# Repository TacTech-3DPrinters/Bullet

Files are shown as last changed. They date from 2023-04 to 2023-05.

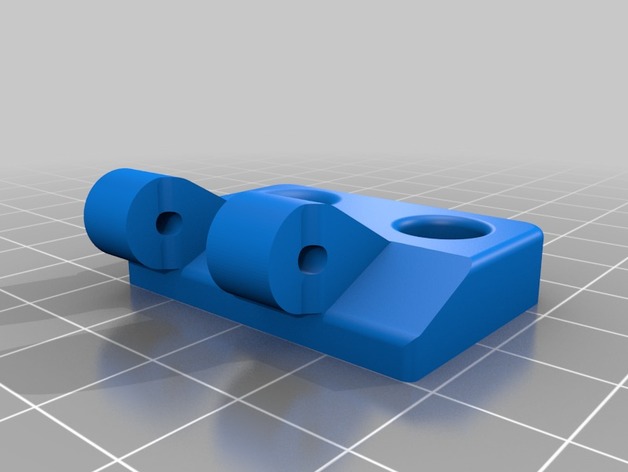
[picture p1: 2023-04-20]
printed-mods/IKEA_Lack_Enclosure_Creality_Ender_3/images/pan_head_left_hand.jpg

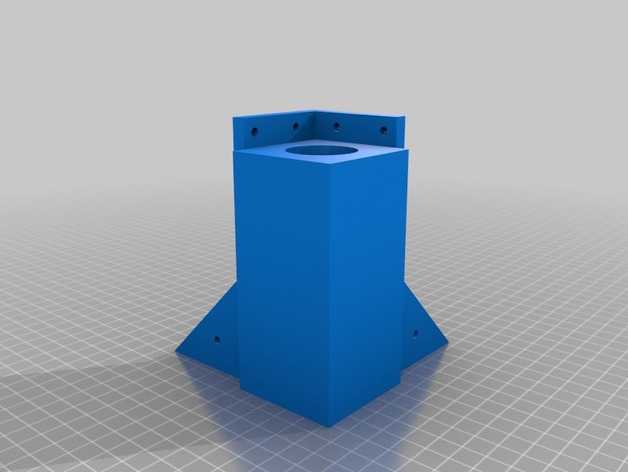
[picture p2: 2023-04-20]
printed-mods/IKEA_Lack_Enclosure_Creality_Ender_3/images/uprights_riser_completed_100mm.jpg

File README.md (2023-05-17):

# Bullet

Bullet is a heavily modified Ender3. All mods and software is tracked on this repository.

Bullet runs Klipper now! It also has two different control boards - the main control board, which is an SKR Mini E3 V1.2 and a toolhead control board connected over CAN, which is a BIQU EBB42. Here are the compiling + deployment instructions moving forward.

## Getting Started

This repo contains all the configs needed for Bullet to run and compile Klipper. Here are the instructions to get started (which may be upgraded to a script in the future:
``` bash
rm -rf $HOME/printer_data/config
ln -s $HOME/Bullet/klipper-configs $HOME/printer_data/config
```
Also will need to re-setup the CAN connection. See https://maz0r.github.io/klipper_canbus/controller/rs485.html

## Main Control Board - SKR Mini E3 V1.2

### Building and Deploying Manually

Run the following commands on the raspberry pi
``` bash
# Build the klipper firmware for the main control board
cd ~/klipper
make clean
make KCONFIG_CONFIG=$HOME/Bullet/control-board/BTT_SKR_Mini_E3_v3/klipper-make.cfg

# Stop the klipper service to upload to the control board
sudo service klipper stop

# Run the flashing script over the SD card
./scripts/flash-sd-card.sh /dev/serial/by-id/usb-Klipper_stm32g0b1xx_4F0047001250415833323520-if00 btt-skr-mini-e3-v3

# Restart the klipper service
sudo service klipper start
```

## Toolhead Board - Biqu EBB42 with MAX31856

### Initialization Steps
1. Set up CAN on Raspberry Pi. See https://maz0r.github.io/klipper_canbus/controller/rs485.html

2. Install CANBoot to allow for installing klipper over CAN

``` bash
# Clone CanBoot
cd ~
git clone https://github.com/Arksine/CanBoot

# Build CanBoot
cd CanBoot
make clean
make KCONFIG_CONFIG=$HOME/Bullet/control-board/BIQU_EBB42_v1_2/canboot-make.config

# Upload CanBoot
# Hold reset and boot buttons while plugged in over USB
# Verify the device is in bootloader mode with:
lsusb
# Flash the CanBoot firmware, make sure you replace the address at the end with what showed up in lsusb
sudo dfu-util -a 0 -D ~/CanBoot/out/canboot.bin --dfuse-address 0x08000000:force:mass-erase:leave -d 0483:df11
# For more information, see source below
```

Source: https://maz0r.github.io/klipper_canbus/toolhead/ebb36-42_v1.1.html

3. Flash Klipper over CAN

``` bash
# Make sure you see the device on the CAN network
~/klippy-env/bin/python ~/klipper/scripts/canbus_query.py can0

# Build the Klipper firmware for the toolhead board
cd ~/klipper
make clean
make KCONFIG_CONFIG=$HOME/Bullet/control-board/BIQU_EBB42_v1_2/klipper-make.config

# Flash the Klipper firmware on the toolhead board over CAN
# Replace the last parameter with the UUID from the canbus_query command above
python3 ~/CanBoot/scripts/flash_can.py -i can0 -f ~/klipper/out/klipper.bin -u 4c6771e6c940
```

Source: https://maz0r.github.io/klipper_canbus/toolhead/ebb36-42_v1.1.html

## Raspberry Pi 3B+
Making sure the Raspberry Pi won't overheat or undervolt due to too little power is super important. Use the following commands to run a worst-case scenaro CPU stress test, each for 10 minutes:

```bash
while true; do vcgencmd measure_clock arm; vcgencmd measure_temp; sleep 10; done& stress -c 4 -t 900s
while true; do vcgencmd measure_clock arm; vcgencmd measure_temp; sleep 10; done& ./cpuburn-a53
```
Source: https://core-electronics.com.au/guides/stress-testing-your-raspberry-pi/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,and%20stability%20of%20the%20system.

## Resources

* Connecting RPI to control board over UART: https://www.youtube.com/watch?v=AtW3GqkKUz8
* CANBUS board + RPI Hat instructions: https://www.youtube.com/watch?v=jgE3XMM9PBk
* Updating klipper on MCU automatically with a script: https://www.youtube.com/watch?v=uNW8phiV83w
* Voron Design documentation for skr mini e3 v1.2: https://docs.vorondesign.com/build/software/miniE3_v12_klipper.html
* Debugging CANBus communication issues: https://www.teamfdm.com/forums/topic/1524-debugging-canbus-and-communication-timeout-while-homingbytes_invalid/
* Sweet KlackEnder probe macros: https://github.com/Harrypulvirenti/Klack-Probe-Macros/tree/main

### Calibrating the 3D Printer
* Preflight checklist: https://github.com/Klipper3d/klipper/blob/master/docs/Config_checks.md
* 

### Board Documentation

* [BigTreeTech SKR E3 Mini V1.2 documentation](https://github.com/bigtreetech/BIGTREETECH-SKR-mini-E3), also found in `control-board/BTT_SKR_MINI_E3_V1_2`
* RS485 CANbus Raspberry Pi Hat: https://www.waveshare.com/rs485-can-hat.htm

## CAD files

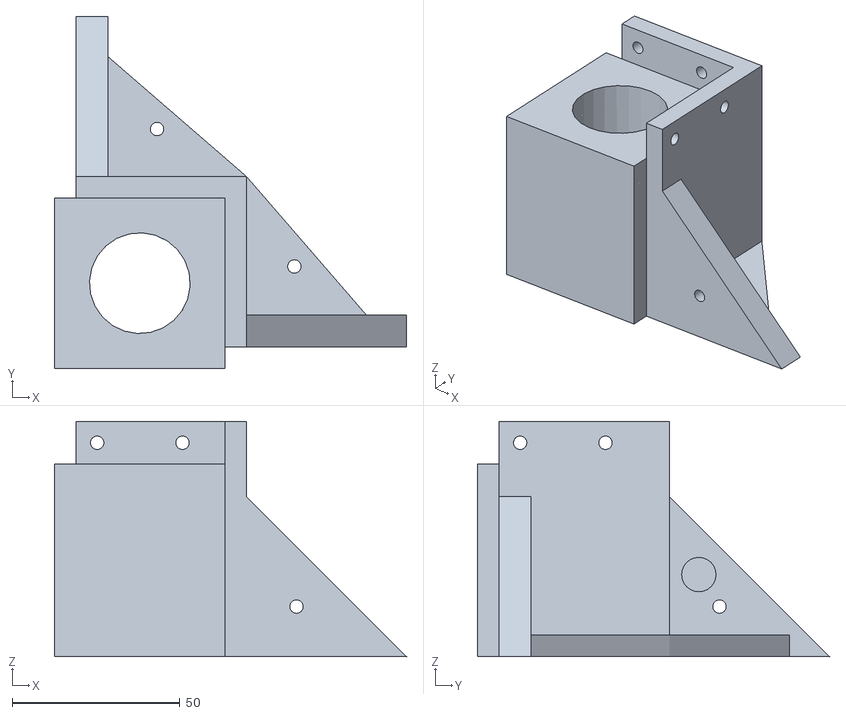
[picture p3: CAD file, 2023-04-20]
printed-mods/IKEA_Lack_Enclosure_Creality_Ender_3/files/uprights_complete_revised_70mm.stl
104.8 x 104.8 x 70.0

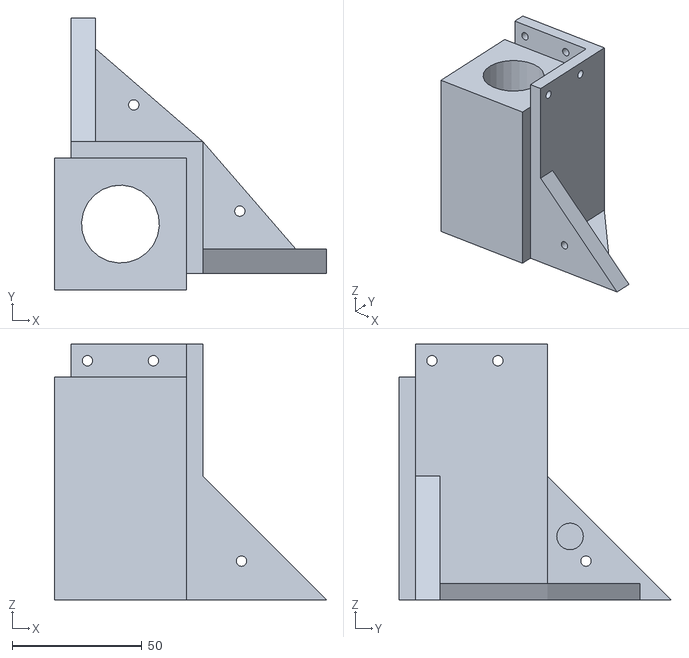
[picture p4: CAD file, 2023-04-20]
printed-mods/IKEA_Lack_Enclosure_Creality_Ender_3/files/uprights_complete_revised.stl
104.8 x 104.8 x 98.4

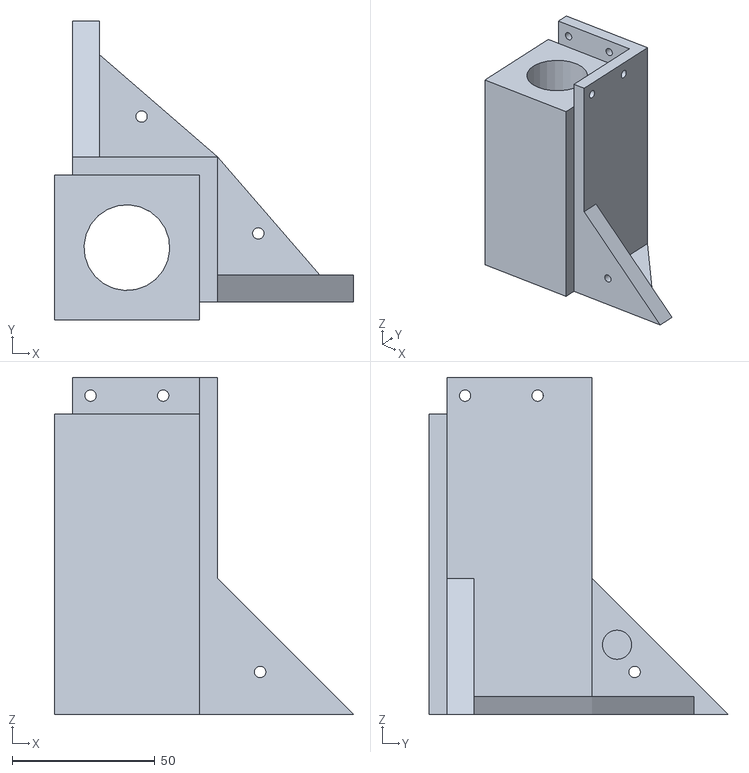
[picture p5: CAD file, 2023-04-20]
printed-mods/IKEA_Lack_Enclosure_Creality_Ender_3/files/uprights_riser_completed_100mm.stl
104.8 x 104.8 x 117.9

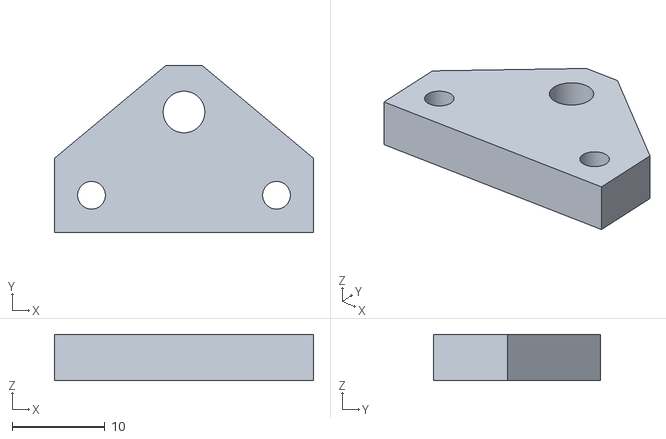
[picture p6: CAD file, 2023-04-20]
IMU_MPU_9265_Mount.stl
28.0 x 18.0 x 5.00

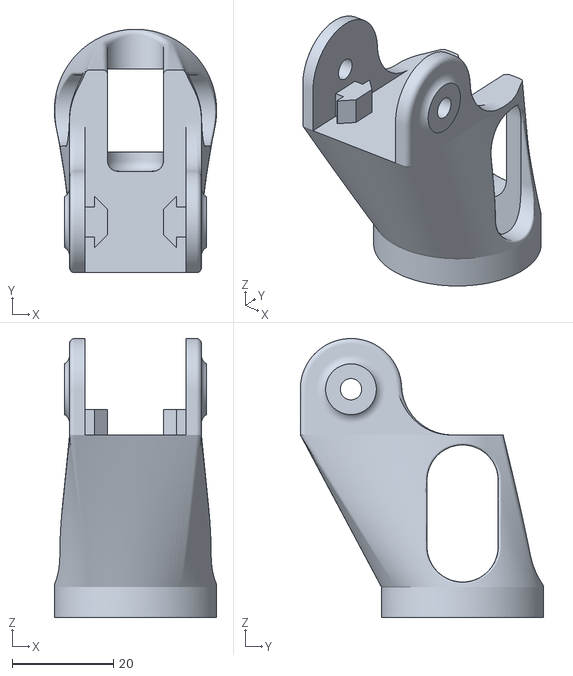
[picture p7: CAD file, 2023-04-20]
printed-mods/BeltTensioners/Ender3_YTensioner_Body.stl
32.0 x 48.0 x 55.0

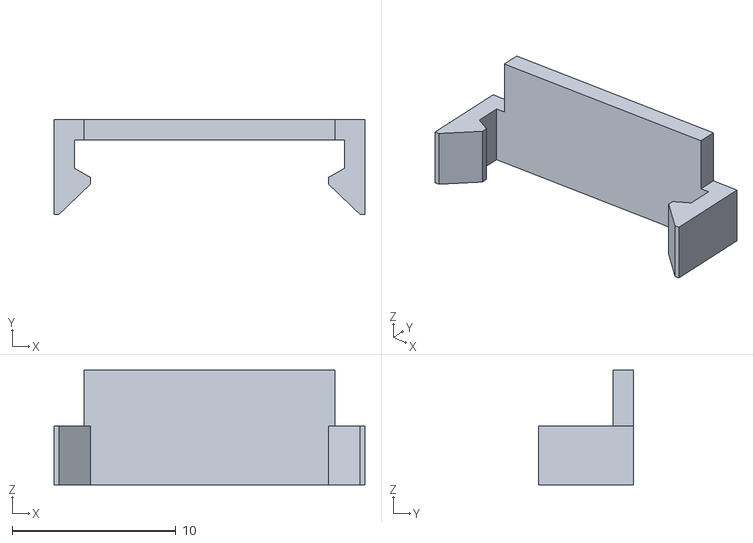
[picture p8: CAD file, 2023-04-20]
printed-mods/CableChain/slim-link_cover.stl
19.0 x 5.80 x 7.00

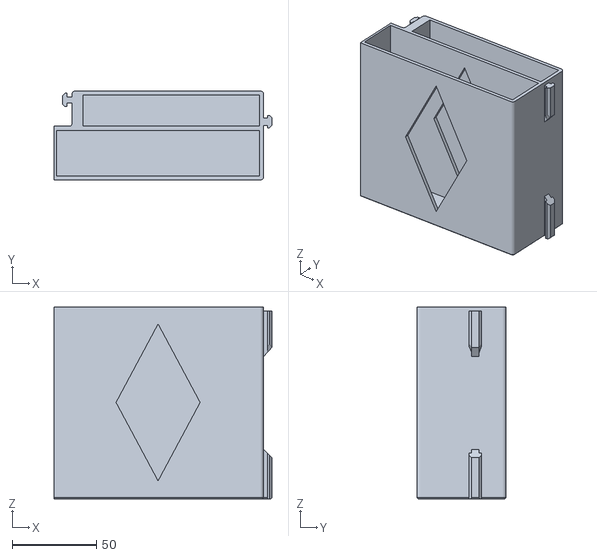
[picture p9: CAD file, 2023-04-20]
printed-mods/Drawers/Drawer_Case_RIGHT.stl
129.6 x 53.0 x 114.0

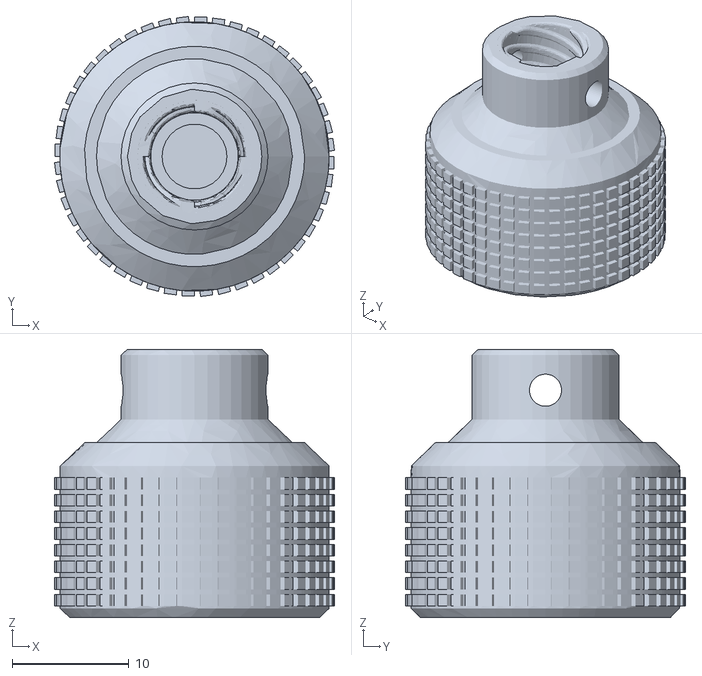
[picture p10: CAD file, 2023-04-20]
printed-mods/Ender3_ZAxis_Knob.stl
24.0 x 24.0 x 23.0

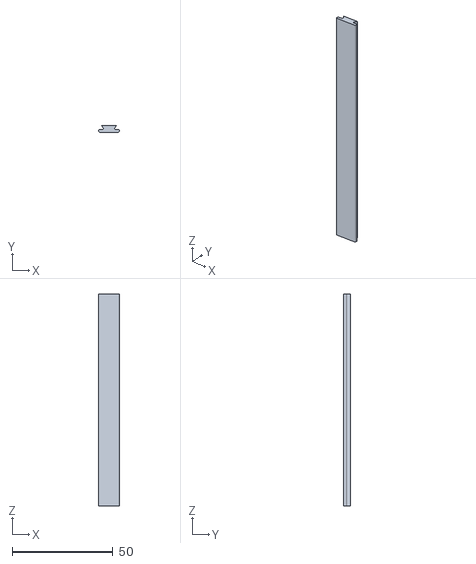
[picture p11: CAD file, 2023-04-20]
printed-mods/Ender_3_V_Slot_Covers/files/slot_cover_105mm.stl
10.2 x 3.23 x 105.0

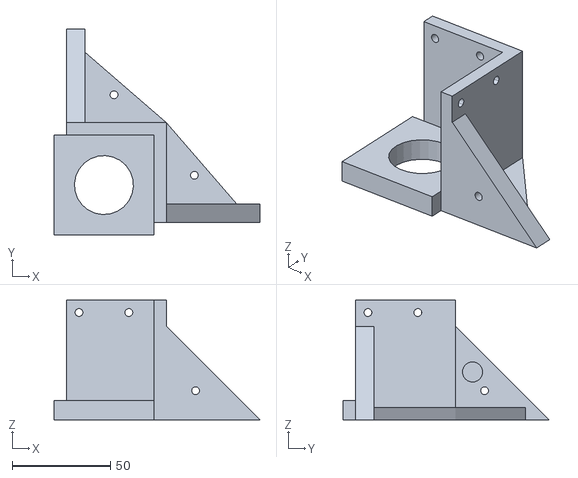
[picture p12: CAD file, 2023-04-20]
printed-mods/IKEA_Lack_Enclosure_Creality_Ender_3/files/uprights_riser_10mm.stl
104.8 x 104.8 x 61.0

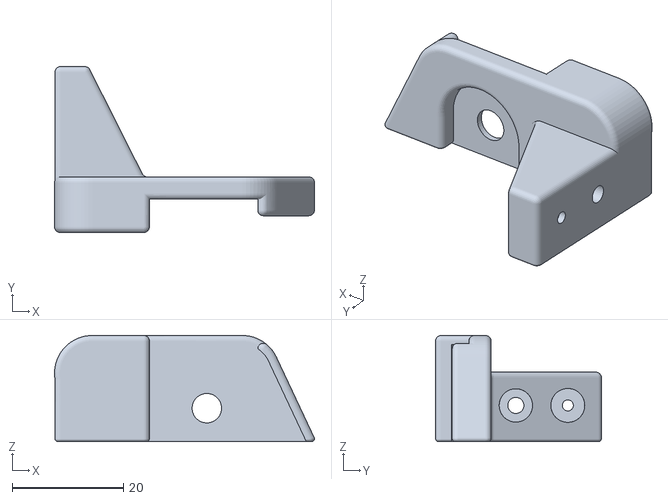
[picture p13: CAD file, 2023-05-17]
printed-mods/KlackEnder-Probe/STL/Ender 3 S1/Probe_Dock_S1.stl
46.8 x 29.9 x 19.1

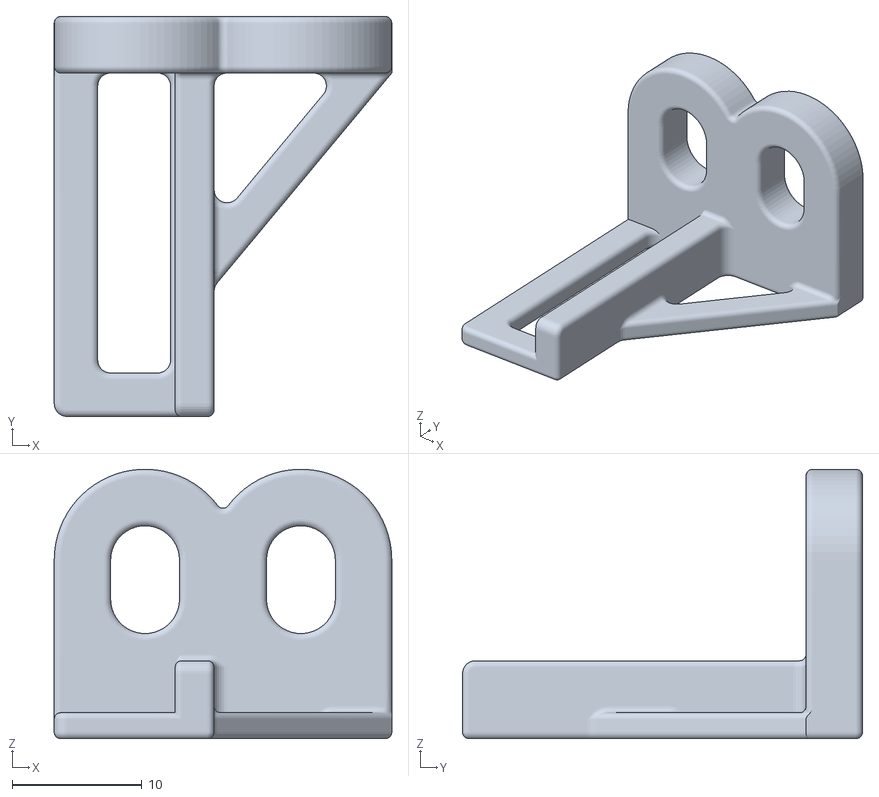
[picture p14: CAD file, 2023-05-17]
printed-mods/KlackEnder-Probe/STL/Probe_Retainer.stl
26.0 x 30.8 x 20.7

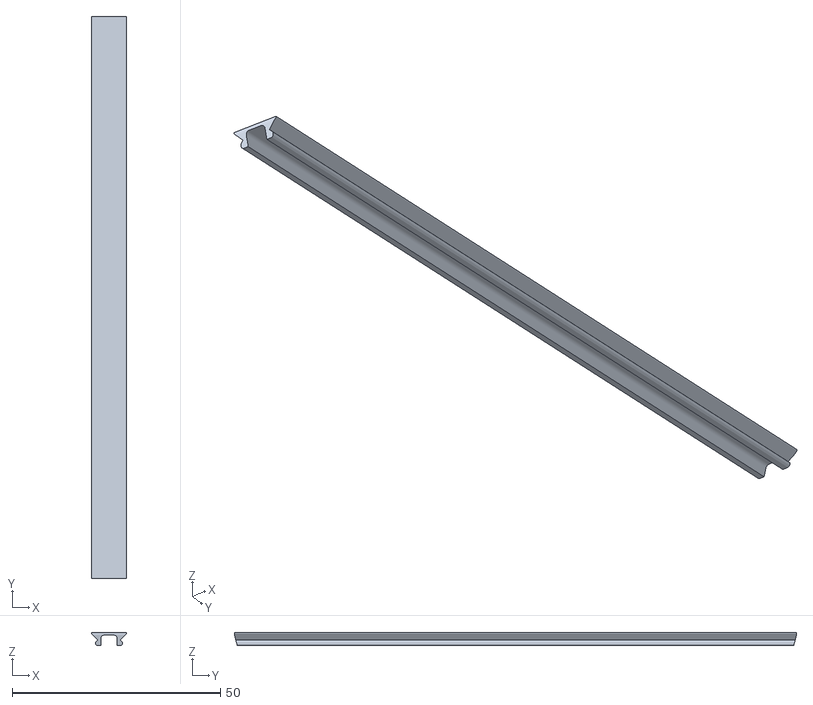
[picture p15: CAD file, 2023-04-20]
printed-mods/LED_Light_Bar/V-Slotcover135mmV2.stl
8.51 x 135.0 x 3.12

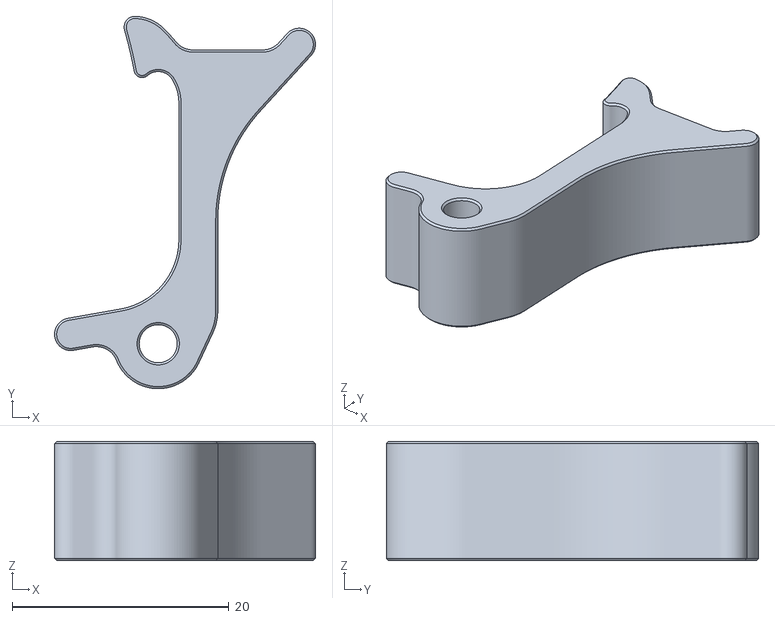
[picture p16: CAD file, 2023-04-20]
printed-mods/VoronAfterburner/[a]_latch.stl
24.1 x 34.3 x 11.0

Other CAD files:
test-prints/temp-tower-190-230.stl
printed-mods/2020Cap.stl
printed-mods/BeltTensioners/Ender3_XTensioner_Center.stl
printed-mods/BeltTensioners/Ender3_XTensioner_Body.stl
printed-mods/BeltTensioners/Ender3_XTensioner_Head.stl
printed-mods/CableChain/cableChain_link_v3.stl
printed-mods/CableChain/extruder-mount-27mm-alu.stl
printed-mods/CableChain/extruder-mount-27mm-stock.stl
printed-mods/CableChain/extruder-mount-32mm-alu-dd.stl
printed-mods/CableChain/slim-link.stl
printed-mods/Drawers/Drawer_Case_LEFT.stl
printed-mods/Ender_3_V_Slot_Covers/files/400mm_for_led_v1.stl
printed-mods/Ender_3_V_Slot_Covers/files/400mm_for_led_v2.stl
printed-mods/Ender_3_V_Slot_Covers/files/slot_cover_143mm_original.stl
printed-mods/Ender_3_V_Slot_Covers/files/slot_cover_165mm.stl
printed-mods/Ender_3_V_Slot_Covers/files/slot_cover_165mm_top_holes.stl
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

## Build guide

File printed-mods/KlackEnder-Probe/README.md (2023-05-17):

## KlackEnder Probe

KlackEnder Probe - **Simple, fast and cheap!**

<table>
  <tr>
    <td> </td>
    <td> </td>
  </tr>
</table>

### What is this about?

Adaptation of the [Klicky](https://github.com/jlas1/Klicky-Probe)/[Quickdraw](https://github.com/Annex-Engineering/Quickdraw_Probe) Probe for the Ender 3 and comparable Creality printers. The probe is compatible with all printers that use the X plate of the Ender 3 and cost of the probe is <10€, of which the switch is the most expensive part.
The probe is compatible with Marlin and Klipper. Both firmwares work with the G29 command, the docking is done automatically by the printer, it couldn't be easier! Both firmwares add a KlackEnder menu to the display that can be used to dock and undock the Probe. The Bed-Mesh can be created via the custom menu, via the default firmware settings or with G29.

### Is it compatible with my printer?

As long as your printer uses a X-Axis plate that's similar to the one of the Ender 3: **YES!***
* You might have to adapt the parts (slightly) if you're not using an Ender 3 or the stock x-plate. See the Basic-Check section to check the basic measurements and see if you printer is compatible. If not and you really struggle with CAD just ping me on my [Discord](https://discord.gg/xqpKrxt9FC) ;)

### Why should I build it?

Well, as with my other mods, the focus is on the best cost-benefit ratio. The KlackEnder is very cheap and very easy to build. No need to pay 40-50€ for a probe that is still affected by heat, takes forever to mesh, and causes a lot of headaches to wire. For the Klack it's: Print - assemble - mount - start printing, that's it. Especially with Klipper, setup couldn't be easier, just use my pre-made macros, copy and paste, hit restart and you're ready for the next print.

#### Quick Overview:

- Compatible with Marlin and Klipper. Easy setup - firmware changes provided.
- 100% automatic probe docking and undocking.
- 100% open source parametric design! With the supported CAD file and instructions, it couldn't be easier to customize the parts to your needs! Even if you've never worked with CAD before, I promise you can customize the parts any way you want!
- Custom menu to control the probe (not for Ender 3 V2 with Jyers GUI).
- The cheapest way to get a fast and very accurate probing ( sample range of 1-2 microsteps (0.000-0.005mm with 16 microsteps)
- Easy to install, no soldering, no complicated wiring
- Works with all pressure surfaces, not affected by heat, no heat soak required

If you have any questions feel free to join the [Discord-Server](https://discord.gg/xqpKrxt9FC).
 
<a href="https://discord.gg/xqpKrxt9FC">
         <img alt="Join" src="https://github.com/kevinakasam/BeltDrivenEnder3/blob/main/_ignore/Pictures/Discord-Logo%2BWordmark-Color.png"
         width=250" >
</a>

#### Parametric CAD Design

I always try my best to support a wide range of possible setups so you don't have to deal with CAD. With this design I have gone one step further: Not only does this design support a wide range of setups, but also the CAD is very easy to adapt for anyone, even if you've never worked with CAD before!

**How that? Parametric design!**

Parametric design means that everything is based on variables / parameters which you can easily change. The design itself adapts automatically to the changes you made. This may still sound a bit complicated, but trust me, with the detailed instructions I provide, it couldn't be easier! More about that on my [website](https://kevinakasam.com/lets-adapt-the-cad/).

## Bill of Materials + Instructions

As for my Belt-Mod, you can find all needed Hardware, STLs and instructions on my Website:

<a href="https://kevinakasam.com/klackender/">
         Guide
</a>

### STL-Files / Tolerances
<table>
  <tr>
    <td> </td>
    <td> </td>
  </tr>
</table>

Some people have contacted me with the problem that the layers split when they insert the magnets. This happens when the magnet is too big for the hole/the hole is too small for the magnet. So either the magnets are a bit bigger than 6mm or your printer prints the holes too small (never use a caliper to measure the magnets!. Only if they are made of plastic!). How the printer prints the holes depends not only on the material (ABS shrinks a bit, while PETG stays fairly constant) but also on the orientation of the holes. Vertical holes are usually a bit smaller than the horizontal ones, the ones that are printed in the walls. This is because these holes are formed by the layers and can never be completely round (the circle is made of 0.2mm (layer height) lines). At the same time, the diameter is strongly influenced by the print settings (speed, acceleration, linear advance/pressure advance, etc.).

However, you may need different tolerances than I do. That is why I have designed a small tolerance test (_thanks to SchlongkyDong for the idea!_). As already described, the tolerances for vertical and horizontal holes can/will differ. Stick a screwdriver through the smaller holes to get your magnets out again.

## Wiring Guide
Since there is no polarity on Switches, it doesn't matter which wire goes where. Just connect the switch to the two marked pins.
In the next chapter about firmware changes you will see where to add the pin.

Wiring for the Rev2 is very easy. Simply unmount/unplug your old z-endstop and connect the probe to the z-endstop port.

## Firmware Guide
The KlackEnder probe works with Marlin and Klipper. This guide only shows you what changes you need to make to the firmware, not how to modify/upload the firmware itself. There are several guides online for different boards and printers.
**You do not have to use the ```Probe In``` or ```Probe Out``` macros.** They're just a nice to have. The printer will do this automatically when you send a ```G29```.

### Klipper

The installation for Klipper is pretty easy. Simply do the changes below and copy the code from the ```KlackEnder.cfg```to your ```printer.cfg```
The ```[gcode_macro G29]``` does the same like the ```[gcode_macro AUTO_BED_MESH]```. I just added this so you can use the G29 command as usual.
#### Changes to the existing config:
```
[stepper_z]
endstop_pin: probe:z_virtual_endstop #if you want to use the Prove as z-endstop (You can unsinstall the stock z endstop then. If not, remive the [homing_override])
#position_endstop: 0 #remove this or uncomment it with a #
position_min: -8 # set a negative value (minimum as the probe z_offset)

[stepper_x]
position_max: 250 #Your printhead have to move all the way to the right to pickup the probe. If your screw collides with the metal plate, simply flip it around.

##Following does not apply for the E3-V2##
[stepper_y]
position_min: -8 #most Ender 3 configs have this wrong. Between the nozzle and the bed is a gap of 8mm (Y dimension) when the printer is homed. If not adapt this and the -8 in the Probe_In Makro). 
position_endstop: -8

```
#### Add new config:

**Don't forgot to edit your probe Pin:**
  ```
  ##################################
## Add this to your printer.cfg ##
##################################
#####################################################################
# KlackEnder- Settings
#####################################################################

# !! Change your Z endstop pin from 'endstop_pin: Pin123' to 'endstop_pin: probe:z_virtual_endstop'
# !! Also add in [stepper_y] 'position_min: -8'. Idk why but most configs mave this wrong. For the Stock Ender 3 the homed Y position is -8.

[probe]
pin: ^PC14 #Probe-Stop Connection on Skr Mini E3 V1.2
z_offset: 0 #Measure per your specific setup
x_offset: 4 # negative = left of the nozzle
y_offset: 21 # negative = in front of of the nozzle
speed: 5.0
lift_speed: 15.0
sample_retract_dist: 1
samples: 2
samples_tolerance_retries: 6

##[(7x7)-1] / 2 = 24
##[(5x5)-1] / 2 = 12
[bed_mesh]
speed: 300
horizontal_move_z: 2
mesh_min: 8,30
mesh_max: 223,201
probe_count: 5,5
relative_reference_index: 12
algorithm: bicubic
fade_start: 1
fade_end: 10
#fade_target:
#   The z position in which fade should converge. When this value is set
#   to a non-zero value it must be within the range of z-values in the mesh.
#   Users that wish to converge to the z homing position should set this to 0.
#   Default is the average z value of the mesh.
split_delta_z: 0.015
#   The amount of Z difference (in mm) along a move that will
#   trigger a split. Default is .025.
move_check_distance: 3
#   The distance (in mm) along a move to check for split_delta_z.
#   This is also the minimum length that a move can be split. Default
#   is 5.0.
mesh_pps: 4,4
#   A comma separated pair of integers (X,Y) defining the number of
#   points per segment to interpolate in the mesh along each axis. A
#   "segment" can be defined as the space between each probed
#   point. The user may enter a single value which will be applied
#   to both axes.  Default is 2,2.
#bicubic_tension: .2
#   When using the bicubic algorithm the tension parameter above
#   may be applied to change the amount of slope interpolated.
#   Larger numbers will increase the amount of slope, which
#   results in more curvature in the mesh. Default is .2.

[homing_override]
set_position_z:0 # Make printer think Z axis is at zero, so we can force a move upwards away from build plate
gcode:
    G90
    G1 Z10 F3000 ; move up to prevent accidentally scratching build plate    
    G28 X
    G28 Y
    PROBE_OUT
    G1 X117 Y117 F6000
    G28 Z
    PROBE_IN

##For Dual Z setups only!! (with independent motors, no Y splitters or dual Z port on board!)##
[z_tilt]
z_positions:
    25,117
    210,117
#   A list of X, Y coordinates (one per line; subsequent lines
#   indented) describing the location of each bed "pivot point". The
#   "pivot point" is the point where the bed attaches to the given Z
#   stepper. It is described using nozzle coordinates (the X, Y position
#   of the nozzle if it could move directly above the point). The
#   first entry corresponds to stepper_z, the second to stepper_z1,
#   the third to stepper_z2, etc. This parameter must be provided.
points:
    4,96.5
    219,96.5
#   A list of X, Y coordinates (one per line; subsequent lines
#   indented) that should be probed during a Z_TILT_ADJUST command.
#   Specify coordinates of the nozzle and be sure the probe is above
#   the bed at the given nozzle coordinates. This parameter must be
#   provided.
speed: 100
#   The speed (in mm/s) of non-probing moves during the calibration.
#   The default is 50.
horizontal_move_z: 15
#   The height (in mm) that the head should be commanded to move to
#   just prior to starting a probe operation. The default is 5.
retries: 10
#   Number of times to retry if the probed points aren't within
#   tolerance.
retry_tolerance: 0.01
#   If retries are enabled then retry if largest and smallest probed
#   points differ more than retry_tolerance. Note the smallest unit of
#   change here would be a single step. However if you are probing
#   more points than steppers then you will likely have a fixed
#   minimum value for the range of probed points which you can learn
#   by observing command output.

#####################################################################
# KlackEnder- Macros
#####################################################################

[gcode_macro PROBE_OUT]
gcode:
    G90
    G1 X245 F4000
    G4 P300
    G1 Z15
    G1 X0

[gcode_macro PROBE_IN]
gcode:
    G90
    G1 Z20
    G1 X245 F20000
    G1 Y-8
    G1 Z0
    G4 P300
    G1 X220 F6000
    G1 Z10
    G1 X0

[gcode_macro AUTO_BED_MESH]
gcode:
    PROBE_OUT
    BED_MESH_CALIBRATE
    #G1 Y0 F20000
    PROBE_IN

[gcode_macro G29]
gcode:
    PROBE_OUT
    BED_MESH_CALIBRATE
    #G1 Y0 F20000
    PROBE_IN

[gcode_macro Accuracy_Test]
gcode:
    PROBE_OUT
    G90
    G1 Y120 X120 F20000
    PROBE_ACCURACY
    PROBE_IN

[gcode_macro AUTO_Z_TILT_ADJUST]
gcode:
    PROBE_OUT
    Z_TILT_ADJUST
    PROBE_IN

#####################################################################
# KlackEnder- Menu - Only if you have a display installed!
#####################################################################

[menu __main]
type: list
name: Main

[menu __main __KlackEnder]
type: list
enable: True
name: KlackEnder

[menu __main __KlackEnder __ProbeOut]
type: command
name: Probe Out
gcode:
    PROBE_OUT

[menu __main __KlackEnder __ProbeIn]
type: command
name: Probe In
gcode:
    PROBE_IN

[menu __main __KlackEnder __AutoBedMesh]
type: command
name: Auto Bed Mesh
gcode:
    G28
    AUTO_BED_MESH
  ```

### Marlin
The installation for Marlin requires some more changes, but I will guide you through this :). These changes are only to get the KlackEnder working correctly. You still need to configure the rest of the options as appropriate for your printer. Support for the KlackEnder and similar probes was only recently added so a current version of Marlin needs to be used. Go to ```https://marlinfw.org/meta/download/``` and download the ```bugfix-2.1.x```. Follow the instructions for downloading, Installing, and configuring VSCode. Before compiling with PlatformIO you will need to setup your config files. Go to ```https://github.com/MarlinFirmware/Configurations/tree/bugfix-2.1.x/config/examples/Creality``` find your Printer/board setup and down load the appropriate Configuration.h & Configuration_adv.h. At this point you will want to go through and make the changes below, once completed you should be good to compile and use your printer. We are working on getting Configuration files posted for common printer combinations as well as .bins uploaded with pre-compiled firmware for common setups.

Marlin will now include a probe deploy and stow option under the motion menu when the Mag_mounted probe is defined.

#### 1. Configuration.h

- Search for ```//#define USE_PROBE_FOR_Z_HOMING``` and uncomment by removing ```//``` before ```#define```
- Search for ```#define PROBE_MANUALLY``` and if not commented out with ```//``` comment it out with ```//```
- If you have plugged your Probe into the Z-Endstop you will need to uncomment ```//#define Z_MIN_PROBE_USES_Z_MIN_ENDSTOP_PIN```
  If you have plugged your Probe into the probe port on your board you don't need to touch this.

- Search for ``` //#define MAG_MOUNTED_PROBE```  uncomment by removing the ```//```
  and change the following lines to
  ```
  #define MAG_MOUNTED_DEPLOY_1 { PROBE_DEPLOY_FEEDRATE, { 245, 114, 20 } }  // Move to side Dock / Attach probe
  #define MAG_MOUNTED_DEPLOY_2 { PROBE_DEPLOY_FEEDRATE, { 200, 114, 020} }  // Move probe off dock
  //#define MAG_MOUNTED_DEPLOY_3 { PROBE_DEPLOY_FEEDRATE, { 245, 114, 20 } }  // lift probe up
  //#define MAG_MOUNTED_DEPLOY_4 { PROBE_DEPLOY_FEEDRATE, {   0,   0,  0 } }  // Extra move if needed
  //#define MAG_MOUNTED_DEPLOY_5 { PROBE_DEPLOY_FEEDRATE, {   0,   0,  0 } }  // Extra move if needed
  #define MAG_MOUNTED_STOW_1   { PROBE_STOW_FEEDRATE,   { 245, 114, 20 } }  // Move to dock
  #define MAG_MOUNTED_STOW_2   { PROBE_STOW_FEEDRATE,   { 245, 114,  0 } }  // Place probe beside remover
  #define MAG_MOUNTED_STOW_3   { PROBE_STOW_FEEDRATE,   { 220, 114,  0 } }  // Side move to remove probe
  #define MAG_MOUNTED_STOW_4   { PROBE_STOW_FEEDRATE,   { 220, 114, 20 } }  // Ensure probe is off
  //#define MAG_MOUNTED_STOW_5   { PROBE_STOW_FEEDRATE,   {   0,   0,  0 } }  // Extra move if needed
  ```
  Probe deploy and stow feed rate can be changed by editing the appropriate lines

- Search for ```NOZZLE_TO_PROBE_OFFSET```  and change
  ```
  #define NOZZLE_TO_PROBE_OFFSET { 10, 10, 0 }

  // Most probes should stay away from the edges of the bed, but
  // with NOZZLE_AS_PROBE this can be negative for a wider probing area.
  #define PROBING_MARGIN 10
  ```

  to

  ```
  #define NOZZLE_TO_PROBE_OFFSET { 8, 21, 1.2 }   //--> set correct offset

  // Most probes should stay away from the edges of the bed, but
  // with NOZZLE_AS_PROBE this can be negative for a wider probing area.
  #define PROBING_MARGIN 15   //--> more clearance to the sides of the bed.
  ```
 
- Search for ```// @section geometry```  and change
  ```
  // The size of the printable area
  #define X_BED_SIZE 200
  #define Y_BED_SIZE 200

  // Travel limits (mm) after homing, corresponding to endstop positions.
  #define X_MIN_POS 0
  #define Y_MIN_POS 0
  #define Z_MIN_POS 0
  #define X_MAX_POS X_BED_SIZE
  #define Y_MAX_POS Y_BED_SIZE
  #define Z_MAX_POS 200
  ```

  For non Ender 3v2's

  ```
  // The size of the printable area
  #define X_BED_SIZE 230    //--> adjust bed size
  #define Y_BED_SIZE 235    //--> adjust bed size

  // Travel limits (mm) after homing, corresponding to endstop positions.
  #define X_MIN_POS 0
  #define Y_MIN_POS -8     //--> adjust endstop position
  #define Z_MIN_POS 0
  #define X_MAX_POS X_BED_SIZE +15     //--> adjust x travel
  #define Y_MAX_POS Y_BED_SIZE
  #define Z_MAX_POS 250     //--> adjust z travel
  ```
  For Ender 3v2's change it to
    ```
  // The size of the printable area
  #define X_BED_SIZE 230    //--> adjust bed size
  #define Y_BED_SIZE 228    //--> adjust bed size

  // Travel limits (mm) after homing, corresponding to endstop positions.
  #define X_MIN_POS 0
  #define Y_MIN_POS 0     //--> adjust endstop position
  #define Z_MIN_POS 0
  #define X_MAX_POS X_BED_SIZE +15     //--> adjust x travel
  #define Y_MAX_POS Y_BED_SIZE
  #define Z_MAX_POS 250     //--> adjust z travel
  ```
 
- Search for ```// @section calibrate```  and change
  ```
  //#define AUTO_BED_LEVELING_3POINT
  //#define AUTO_BED_LEVELING_LINEAR
  //#define AUTO_BED_LEVELING_BILINEAR
  //#define AUTO_BED_LEVELING_UBL
  //#define MESH_BED_LEVELING

  /**
  * Normally G28 leaves leveling disabled on completion. Enable one of
  * these options to restore the prior leveling state or to always enable
  * leveling immediately after G28.
  */
  //#define RESTORE_LEVELING_AFTER_G28
  //#define ENABLE_LEVELING_AFTER_G28
  ```

  to

  ```
  //#define AUTO_BED_LEVELING_3POINT
  //#define AUTO_BED_LEVELING_LINEAR
  //#define AUTO_BED_LEVELING_BILINEAR
  #define AUTO_BED_LEVELING_UBL     //--> Remove //
  //#define MESH_BED_LEVELING

  /**
  * Normally G28 leaves leveling disabled on completion. Enable one of
  * these options to restore the prior leveling state or to always enable
  * leveling immediately after G28.
  */
  #define RESTORE_LEVELING_AFTER_G28    //--> Remove //
  //#define ENABLE_LEVELING_AFTER_G28
  ```
 
- Search for ```Unified Bed Leveling```  
  Change  from ```#define MESH_INSET 1``` to ```#define MESH_INSET 10```
  Change   ```#define GRID_MAX_POINTS_X 10``` to ```#define GRID_MAX_POINTS_X 15```  
  Uncomment  by removing the ```//``` before ```#define UBL_MESH_WIZARD```  
  Uncomment  ```//#define LCD_BED_LEVELING```  
  Uncomment  ```//#define LCD_BED_TRAMMING```  
  Uncomment  ```//#define BED_TRAMMING_USE_PROBE```  
  Uncomment  ```//#define Z_SAFE_HOMING```  
  Uncomment  ```//#define EEPROM_INIT_NOW   // Init EEPROM on first boot after a new build```  

 - In Configuration_adv.H
  Uncomment ```//#define PROBE_OFFSET_WIZARD```

  ## Marlin Setup Before printing
  Go into the menu->Motion->Unified Bed Leveling->UBL Custom Bed Mesh
  set your normal bed temp and hotend temp and then select custom mesh. This will probe all points that can be reached by the probe and then interpolate the rest.
  
  ## Marlin Slicer Start Gcode
  In your slicer Gcode look for a line that says 
  ```G28```
  after that line add in the following two lines
  ```
  G29 L0 ; load mesh saved in slot 0 which is the default slot
  G29 A ; activate bed mesh leveling.
  G29 J ; Probe 3 points and tilt the mesh loaded in slot 0 to match the current bed tilt
  ```

### Rev_1 vs. Rev_2 (and Rev_2.x)

What's the difference between Revision 1 and Revion 2?
                   
The most important difference is the position of the probe. With the Rev2, the probe is attached to the X-axis, which is why the probe can be used as a Z end stop. So no additional port for an end stop is needed and the probe can simply be connected to the old Z endstop port. The renders below show the difference, the upper one is the Rev2. (The Probe mount on the hotendplate is the same for both version)
                   
<table>
  <tr>
    <td><img src="https://github.com/kevinakasam/KlackEnder-Probe/blob/main/Archive/Rev_2/Images/Comp.png" width="450"> </td>
    <td><img src="https://github.com/kevinakasam/KlackEnder-Probe/blob/main/Archive/Rev_2/Images/Comp2.png" width="450"> </td>
  </tr>
</table>

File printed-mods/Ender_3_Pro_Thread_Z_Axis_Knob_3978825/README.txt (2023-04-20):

Ender 3 Pro Thread Z Axis Knob by 3HappyOwls on Thingiverse: https://www.thingiverse.com/thing:3978825

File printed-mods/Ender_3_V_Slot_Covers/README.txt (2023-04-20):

Ender 3 Pro V-Slot covers by ximes on Thingiverse: https://www.thingiverse.com/thing:3379068

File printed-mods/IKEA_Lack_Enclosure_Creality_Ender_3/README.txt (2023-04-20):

IKEA Lack Enclosure Creality Ender 3 Compilation by Woody1978 on Thingiverse: https://www.thingiverse.com/thing:3083358

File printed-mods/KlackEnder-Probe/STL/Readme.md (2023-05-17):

All parts can be printed without supports. Just print them in the provided orientation.

**Print the tolerance test first!**
All horizontal holes have a tolerance of 0.2mm, all vertical ones have no tolerance. This should fit most printers and give you a tight fit. If the fit isn't right use the provided CAD files to change the tolerance. The f3d file has paramters for that (Check out my [website](https://kevinakasam.com/lets-adapt-the-cad/)). You could also join the discord and I will send you a file with the tolerances you want.

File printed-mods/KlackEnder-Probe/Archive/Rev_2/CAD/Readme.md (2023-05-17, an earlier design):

All supported Step and Fusion 360 files. Feel free to modify the parts, but please upload them as remix to Thingiverse :)

Original file link:
Ender 3 Step: https://github.com/Creality3DPrinting/Ender-3/tree/master/Ender-3%20Mechanical

# How to change the tolerances

There is an f3d file in the CAD folder. This file format is for Autodesk Fusion 360, a free CAD program for private users. You can use it to adjust the tolerances if the STL files I provided do not fit.
As described in the tolerance test, there are different tolerances for vertical and horizontal holes. Follow the steps below to create your own STL.

## 1: Open the fusion file
First you have upload the file to fusion. Simply double click on the file or upload it to the browser in fusion on the left side (once you opended a folder e.g `My First Project` theres a small blue upload option at the very top). Then open the file, it should look close to this:



## 2: Open the parameters tab

Click on the `MODIFY`dropdown and select the parameters option.



## 3: Change the parameters

Double click on the value you want to change.



## 4: Find the file you want to export

Find the file you want to export in the browser on the left side. You can expand the folders by clicking on the small triangles. (You can also double click on the file in the CAD window, right click on it and select `Find In Browser`at the very end of the menu).



## 5: Export the STL

Once you found the file you want to export, right click on it and select `Save As Mesh`.



## 6: Save the STL

Simply confirm the small dialog on the right by clicking `OK`. Select a place on you PC to save it, that's all :)



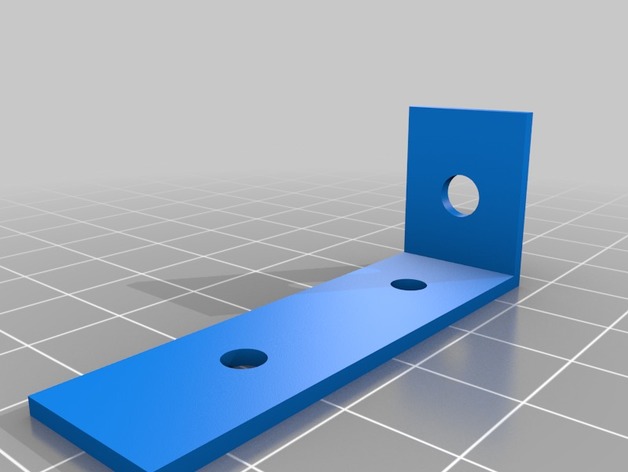
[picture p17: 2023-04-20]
printed-mods/IKEA_Lack_Enclosure_Creality_Ender_3/images/24V_PSU_holder.jpg

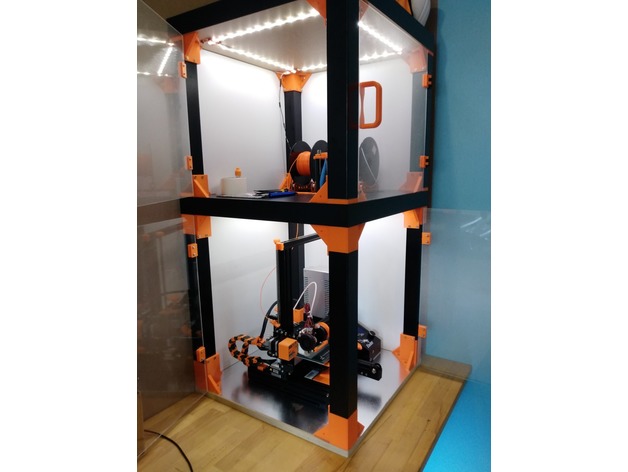
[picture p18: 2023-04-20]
printed-mods/IKEA_Lack_Enclosure_Creality_Ender_3/images/d2b5ca33bd970f64a6301fa75ae2eb22.jpg

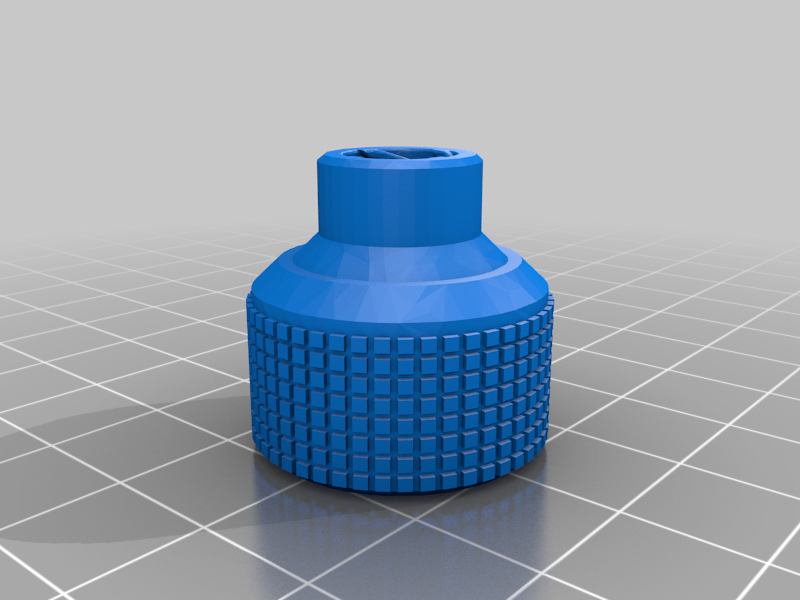
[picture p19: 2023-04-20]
printed-mods/Ender_3_Pro_Thread_Z_Axis_Knob_3978825/images/Ender3Pro_Threaded_Z_Axis_Knob.png

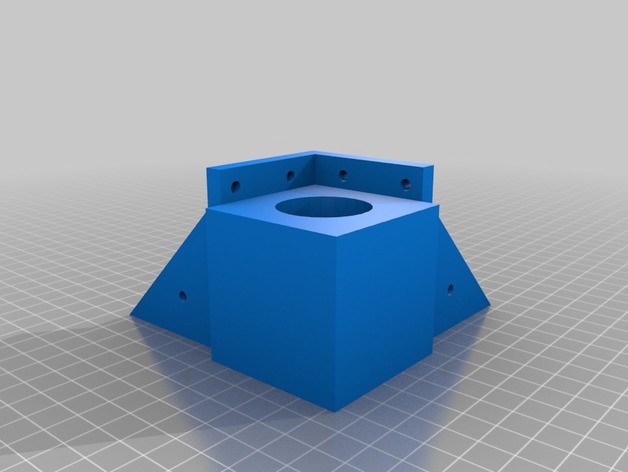
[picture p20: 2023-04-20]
printed-mods/IKEA_Lack_Enclosure_Creality_Ender_3/images/uprights_riser_50mm.jpg

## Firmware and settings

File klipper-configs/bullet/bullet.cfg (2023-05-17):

###########################################
########## Bullet Printer Config ##########
###########################################

# Include MainBoard
[include btt_skr_mini_e3_v3.cfg]

# Include Toolhead board
[include biqu_ebb42.cfg]

# Include RPI 3 Configuration
[include rpi3.cfg]

# Include g-code macros:
[include macros.cfg]

# Include KlackEnder macros
[include klackender.cfg]

# Include Accelerometer for input shaping
# comment out when not in use
# [include accel_mcu.cfg ]

#########################
##### Main Settings #####
#########################
[printer]
kinematics: cartesian
max_velocity: 300
max_accel: 3000
max_z_velocity: 5
max_z_accel: 100

# Controller Fan
[temperature_fan _controller_fan]
sensor_type: temperature_host
target_temp: 60
max_speed: 0.8
min_speed: 0.0
control: watermark
max_delta: 5
min_temp: 0
max_temp: 85

####################
##### Extruder #####
####################
[extruder]
rotation_distance: 23.500
gear_ratio: 3:1
nozzle_diameter: 0.600
filament_diameter: 1.750
sensor_type: NTC 100K MGB18-104F39050L32
control: pid
pid_Kp: 22.094
pid_Ki: 1.023
pid_Kd: 119.305
min_temp: 0
max_temp: 280
min_extrude_temp: 0
pressure_advance: 0.045

[heater_fan hotend_fan]
heater: extruder
heater_temp: 50
fan_speed: 0.8

[fan]
max_power: 1.0

######################
##### Heated Bed #####
######################
[heater_bed]
sensor_type: ATC Semitec 104GT-2
control: pid
pid_Kp: 70.445
pid_Ki: 0.968
pid_Kd: 1281.210
min_temp: 0
max_temp: 130

#################################
##### Z Home / Bed Leveling #####
#################################

[homing_override]
axes: z
set_position_z: 0
gcode:
    G90                 ; Absolute positioning
    G1 Z5 F3000         ; move up to prevent accidentally scratching build plate

    {% if printer.toolhead.homed_axes != "xyz" %}
        ; Test against xyz (not xy) because we assert z=0 at the beginning (set_position_z: 0)
        G28 X Y         ; Home X and Y
    {% endif %}

    PROBE_OUT
    G1 X98 Y85 F6000    ; Move to home Z position
    G28 Z               ; Home Z
    PROBE_IN

[probe]
pin: ^EBBCan: PB6
x_offset: 19
y_offset: 32
z_offset: 1.35
speed: 2.5
lift_speed: 15.0
sample_retract_dist: 1.0
samples: 2

[bed_mesh]
speed: 100
horizontal_move_z: 5
mesh_min: 25, 25
mesh_max: 210, 210
probe_count: 5,5
fade_start: 1
fade_end: 10
fade_target: 0

[z_tilt]
# Positions/points were chosen based on the probing position to be
#   - aligned with the bed mounting screws in the +/- X direction
#   - between the bed mounting screws in the +/- Y direction, same as probe y_offset
z_positions:
    -30, 85
    265, 85
points:
    15, 85
    185, 85
speed: 100
horizontal_move_z: 5
retries: 20
retry_tolerance: 0.01

###################################
#### Additional Stepper Motor #####
###################################
[stepper_x]
rotation_distance: 40
position_endstop: -15
position_min: -15
position_max: 235
homing_speed: 50

[stepper_y]
rotation_distance: 40
position_endstop: -15
position_min: -15
position_max: 220
homing_speed: 50

[stepper_z]
rotation_distance: 8
position_min: -6
position_max: 200
endstop_pin: probe:z_virtual_endstop

[stepper_z1]
rotation_distance: 8

#######################
##### Other Stuff #####
#######################

# Overhead lights
[neopixel overhead_lights]
chain_count: 13
color_order: GRB
initial_RED: 0.9
initial_GREEN: 0.9
initial_BLUE: 0.9

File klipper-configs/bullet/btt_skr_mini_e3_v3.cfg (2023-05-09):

# This file contains common pin mappings for the BIGTREETECH SKR mini
# E3 v3.0. To use this config, the firmware should be compiled for the
# STM32G0B1 with a "8KiB bootloader" and USB communication/USART.

# The "make flash" command does not work on the SKR mini E3. Instead,
# after running "make", copy the generated "out/klipper.bin" file to a
# file named "firmware.bin" on an SD card and then restart the SKR
# mini E3 with that SD card.

# See docs/Config_Reference.md for a description of parameters.

[mcu]
serial: /dev/serial/by-id/usb-Klipper_stm32g0b1xx_4F0047001250415833323520-if00

[temperature_sensor mcu_temp_sensor]
sensor_type: temperature_mcu
sensor_mcu: mcu

# [bltouch]
# sensor_pin: PC14
# control_pin: PA1

###################
##### X Motor #####
###################
[stepper_x]
step_pin: PB13
dir_pin: !PB12
enable_pin: !PB14
microsteps: 16
rotation_distance: 40
endstop_pin: ^PC0

[tmc2209 stepper_x]
uart_pin: PC11
tx_pin: PC10
uart_address: 0
run_current: 0.580
hold_current: 0.500
stealthchop_threshold: 999999

###################
##### Y Motor #####
###################
[stepper_y]
step_pin: PB10
dir_pin: !PB2
enable_pin: !PB11
microsteps: 16
rotation_distance: 40
endstop_pin: ^PC1

[tmc2209 stepper_y]
uart_pin: PC11
tx_pin: PC10
uart_address: 2
run_current: 0.580
hold_current: 0.500
stealthchop_threshold: 999999

###################
##### Z Motor #####
###################
[stepper_z]
step_pin: PB0
dir_pin: PC5
enable_pin: !PB1
microsteps: 16
rotation_distance: 8

[tmc2209 stepper_z]
uart_pin: PC11
tx_pin: PC10
uart_address: 1
run_current: 0.580
hold_current: 0.500
stealthchop_threshold: 999999

##########################
##### Extruder Motor #####
##########################
# These are normally extruder
[stepper_z1]
step_pin: PB3
dir_pin: PB4
enable_pin: !PD1
microsteps: 16
rotation_distance: 8

[tmc2209 stepper_z1]
uart_pin: PC11
tx_pin: PC10
uart_address: 3
run_current: 0.3
hold_current: 0.2
stealthchop_threshold: 999999

##############################
##### Extruder / Heatbed #####
##############################

# [extruder]
# heater_pin: PC8
# sensor_pin: PA0

[heater_bed]
heater_pin: PC9
sensor_pin: PC4

#############################
##### Fan Configuration #####
#############################
# FAN 0:
# [heater_fan e0_hotend_fan]
# pin: PC6

# FAN 1:
# [fan]
# pin: PC7

# FAN 2:
[temperature_fan _controller_fan]
pin: PB15

######################################
##### Extra Board Configurations #####
######################################

[neopixel overhead_lights]
pin: PA8

[board_pins]
aliases:
    # EXP1 header
    EXP1_1=PB5,  EXP1_3=PA9,   EXP1_5=PA10, EXP1_7=PB8, EXP1_9=<GND>,
    EXP1_2=PA15, EXP1_4=<RST>, EXP1_6=PB9,  EXP1_8=PD6, EXP1_10=<5V>

# BTT Display Configuration
[display]
lcd_type: emulated_st7920
spi_software_miso_pin: PD8 # status led, Virtual MISO
spi_software_mosi_pin: PD6
spi_software_sclk_pin: PB9
en_pin: PB8
encoder_pins: ^PA10, ^PA9
click_pin: ^!PA15

[output_pin beeper]
pin: PB5

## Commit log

2022-07-10 Initial commit with clone of Marlin Repo
2022-07-11 add old + new firmware
    [Configuration.h, Configuration_adv.h, esp32.csv]
2022-07-11 Moved to use old firmware revision
    don't want to do the work to upgrade right now
    [Configuration.h, Configuration_adv.h, esp32.csv]
2022-07-11 Add fw config changes after afterburner upgrade
    [Configuration.h]
2022-07-11 Add final config changes to bed leveling and centering
    [Configuration.h]
2023-04-20 Add printed mods and test prints
    [2020Cap.stl, 24V_PSU_Cover_v3.stl, 24V_PSU_holder.stl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]
2023-05-04 Remove marlin firmware and add klipper configs instead
    [Configuration.h, Configuration_adv.h, accel_mcu.cfg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]
2023-05-07 Add rs485 CAN hat user manuals and schematics
2023-05-07 Add documentation for the skr mini e3 v1.2
    [klipper-make.cfg]
2023-05-09 Move skr mini e3 v1.2 files into directory and add klipper make config for it
2023-05-09 Add ebb42 canboot and klipper make configs
2023-05-09 Add skr mini e3 v3 klipper make config and README instuctions + documentation
2023-05-09 Add new CAN toolhead board with working configs!
    [biqu_ebb42.cfg, btt_skr_mini_e3_v3.cfg, bullet.cfg]
2023-05-11 Fix extruder settings and add klicky probe settings with safe z home
    [biqu_ebb42.cfg, bullet.cfg]
2023-05-11 Add z-tilt adjustment settings
    [bullet.cfg]
2023-05-11 Add bed mesh setup
    [bullet.cfg]
2023-05-11 Add in klicky automation and combine with existing macros
    [bullet.cfg, klackender.cfg, macros.cfg]
2023-05-11 Add z offset calibration + script
    [bullet.cfg, klackender.cfg, macros.cfg]
2023-05-16 Add klackEnder probe hardware files
    [KlackEnder.cfg, KlackEnderRev2.cfg, Probe_Block v0.15 h0.15.stl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]
2023-05-17 Add recent changes
    [bullet.cfg, macros.cfg]
